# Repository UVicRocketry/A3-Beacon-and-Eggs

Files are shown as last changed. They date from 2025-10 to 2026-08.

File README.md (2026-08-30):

# A3 Beacon and Eggs

Hardware design files (KiCad 9) for the A3 recovery beacon — a VHF transmitter
stitched to the main recovery shock chord.

<p align="center">
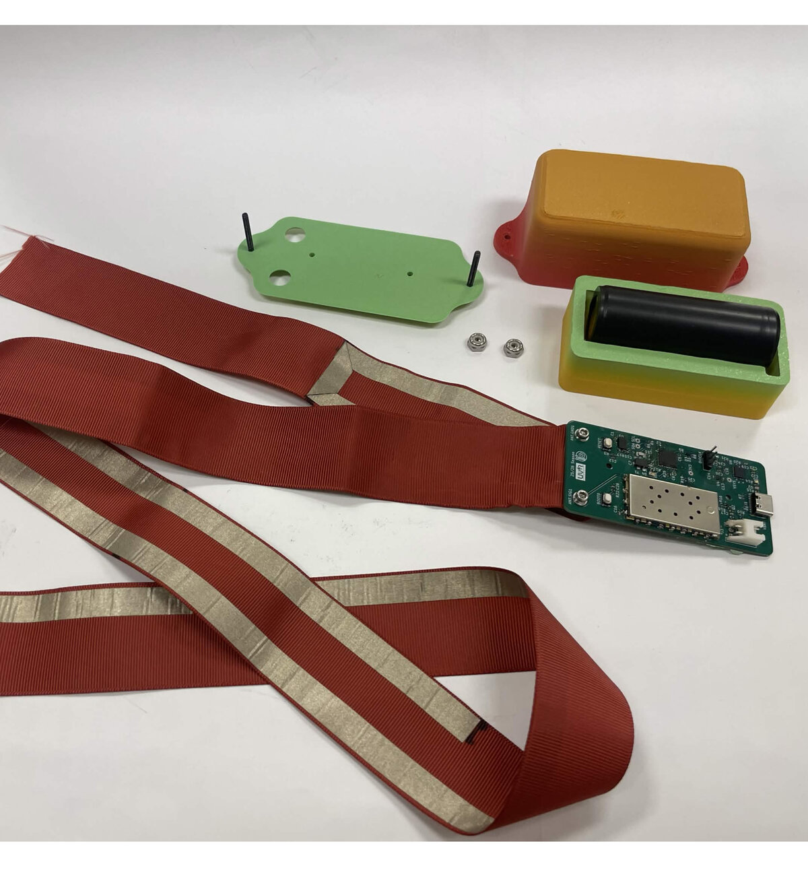
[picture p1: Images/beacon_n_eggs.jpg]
Assembled V1 beacon bolted to its fabric antenna strap, with the printed enclosure and 18650 holder
  
</p>

## Boards

### `Beacon_and_eggs/` — V1 (fabricated)

40 × 80 mm, 4-layer (F.Cu / GND / PWR / B.Cu).

- **MCU** — STM32F411CEU6 with 25 MHz and 32.768 kHz crystals, SWD header,
  boot/reset circuits, and test points
- **Radio** — SA868S / SA818V VHF module, UART control at 9600 baud, with
  TX_EN and TX_PWR_DN control lines and a TX audio input
- **Sensor** — ADXL343 accelerometer on I²C (ALT ADDRESS tied high → 0x1D)
- **Power** — BQ24070 Li-ion charger, USB-C input with ESD clamps, MIC5528
  3.3 V LDO, NTA4151P / NTA4153N load switches, and a divider for battery
  voltage monitoring on the ADC
- **Antenna** — plated mounting holes serve as the RF feed and ground clamp
  for a fabric antenna. 
- Status LEDs, battery connector, and an interactive BOM under `bom/`

### `Beacon_and_eggs_V2/` — in progress

A condensed second revision. Planned:

- Moved to low frequency LoRa Module with Semtech's SX1278
- Move to a smaller Battery
- PIC MCU to interface with transmitter

WIP

### `Beacon BNC Adapter PCB/`

Two-connector coax breakout, used to attach a standard antenna or analyzer to
the beacon's bare antenna pads for bench testing.

## Firmware

Lives in the separate [A3_Beacon_and_Eggs_FW](https://github.com/zgsdlv/A3_Beacon_and_Eggs_FW)
repository (STM32CubeMX + HAL). It is bring-up code only, written to check that
the V1 hardware works - it reads the accelerometer's ID register, handshakes
with the SA868S, and blinks out which of the two responded.

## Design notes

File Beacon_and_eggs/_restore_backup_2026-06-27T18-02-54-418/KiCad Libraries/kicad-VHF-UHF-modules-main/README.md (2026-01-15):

This repository contains symbols, footprints and a 3D model for VHF/UHF modules such as the Dorji [DRA818V](https://www.dorji.com/products-detail.php?ProId=55)/[DRA818U](https://www.dorji.com/products-detail.php?ProId=56) and the SA818, SA818S, SA686 and SA868S modules by [NiceRF](https://www.nicerf.com/).

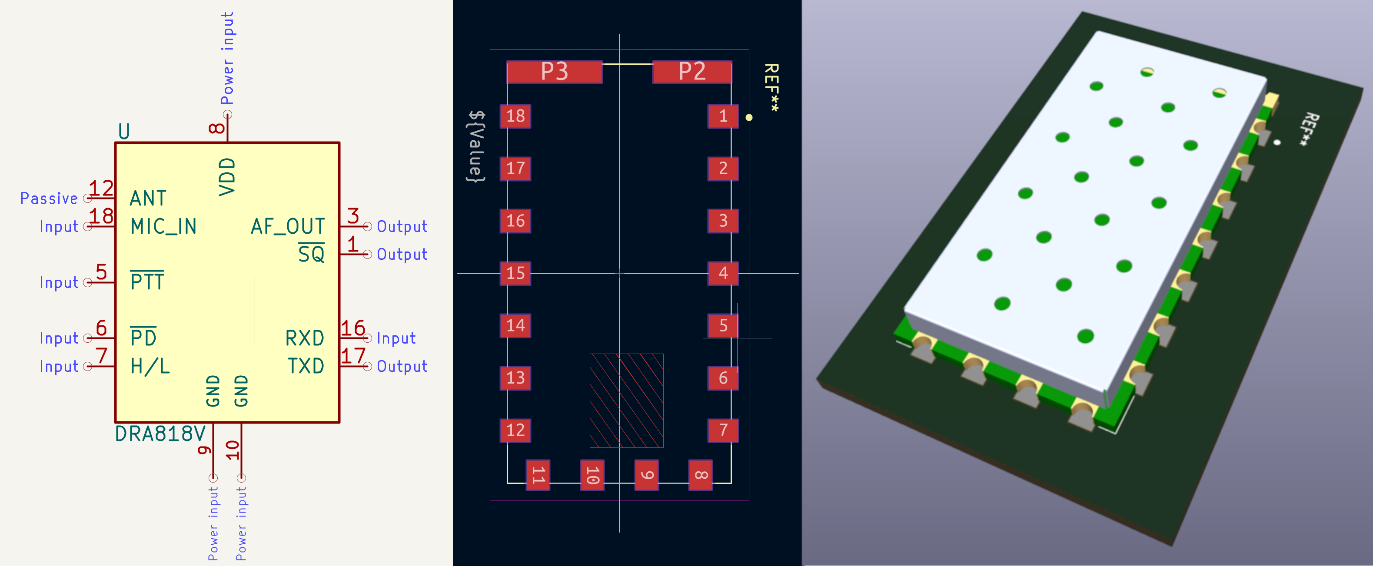
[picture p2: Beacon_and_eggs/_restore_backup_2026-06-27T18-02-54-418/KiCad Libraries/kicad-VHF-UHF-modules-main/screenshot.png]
Screenshots


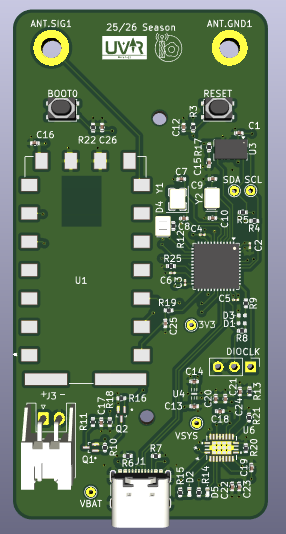
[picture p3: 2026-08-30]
Images/Beacon_and_eggs_3D_View.png

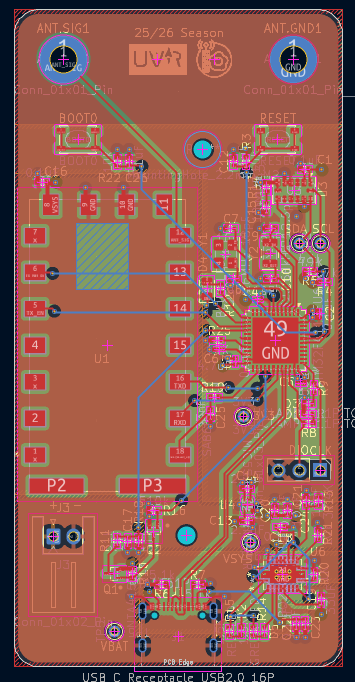
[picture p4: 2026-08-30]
Images/Beacon_PCB_Layout.png

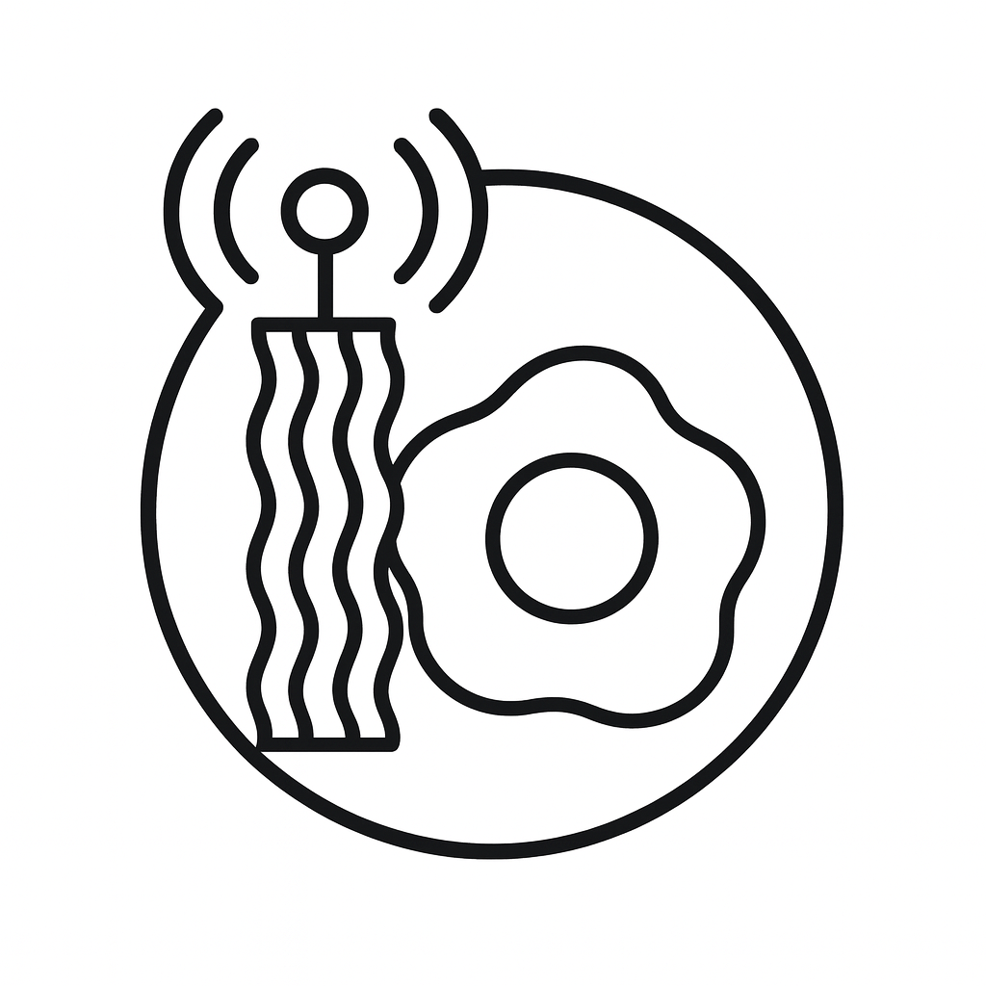
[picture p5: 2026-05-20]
Beacon_and_eggs/_restore_backup_2026-06-27T18-02-54-418/Images/beacon_and_eggs.png

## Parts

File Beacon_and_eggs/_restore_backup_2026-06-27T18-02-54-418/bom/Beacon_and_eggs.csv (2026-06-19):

Id | Designator | Footprint | Quantity | Designation | Supplier and ref
1 |  |  | 1
2 | ANT.GND1, ANT.SIG1 | MountingHole_3.2mm_M3_DIN965_Pad_TopBottom | 2 | Conn_01x01_Pin
3 | BOOT0 | SW_SPST_PTS810 | 1 | BOOT0
4 | C1, C12, C16, C18, C20, C22, C26 | C_0402_1005Metric | 7 | 0.1uF
5 | C2, C3, C4, C5 | C_0201_0603Metric | 4 | 0.1uF
6 | C6 | C_0201_0603Metric | 1 | 4.7uF
7 | C7, C8 | C_0402_1005Metric | 2 | 16pF
8 | C9, C10 | C_0402_1005Metric | 2 | 5pF
9 | C13, C14 | C_0402_1005Metric | 2 | 2.2uF
10 | C15, C21, C23 | C_0402_1005Metric | 3 | 10uF
11 | C17 | C_0402_1005Metric | 1 | 1nF
12 | C19 | C_0402_1005Metric | 1 | 33uF
13 | C24 | C_0402_1005Metric | 1 | 10nF
14 | C25 | C_0402_1005Metric | 1 | 33nF
15 | D1, D3 | D_0402_1005Metric | 2 | UCLAMP3311P.TCT
16 | D2 | LED_0402_1005Metric | 1 | RED LED
17 | D4 | LED_0805_2012Metric | 1 | BLUE LED
18 | D5 | LED_0402_1005Metric | 1 | GREEN LED
19 | J1 | USB_C_Receptacle_GCT_USB4105-xx-A_16P_TopMnt_Horizontal | 1 | USB_C_Receptacle_USB2.0_16P
20 | J3 | JST_XH_S2B-XH-A_1x02_P2.50mm_Horizontal | 1 | Conn_01x02_Pin
21 | Q1 | SOT50P160X90-3N | 1 | NTA4151P
22 | Q2 | SOT50P160X90-3N | 1 | NTA4153N
23 | R3, R21, R22 | R_0402_1005Metric | 3 | 10k
24 | R4, R5 | R_0402_1005Metric | 2 | 4.7k
25 | R6, R7 | R_0402_1005Metric | 2 | 5.1k
26 | R8, R9, R12 | R_0402_1005Metric | 3 | 250R
27 | R10, R11, R18 | R_0402_1005Metric | 3 | 51k
28 | R13 | R_0402_1005Metric | 1 | 37.4K
29 | R14, R15 | R_0402_1005Metric | 2 | 1.5K
30 | R16 | R_0402_1005Metric | 1 | 510k
31 | R17 | R_0402_1005Metric | 1 | 50R
32 | R19 | R_0402_1005Metric | 1 | 3.3K
33 | R20 | R_0402_1005Metric | 1 | 1K
34 | R25 | R_0402_1005Metric | 1 | 10K
35 | RESET | SW_SPST_PTS810 | 1 | RESET
36 | U1 | VHF_UHF_Module_generic | 1 | SA868S
37 | U2 | QFN-48-1EP_7x7mm_P0.5mm_EP5.6x5.6mm | 1 | STM32F411CEU6TR
38 | U3 | LGA-14_3x5mm_P0.8mm_LayoutBorder1x6y | 1 | ADXL343
39 | U4 | XTDFN6_1P2X1P2_MCH | 1 | MIC5528-3.3YMX-TR
40 | U6 | RHL20_2P05X3P05 | 1 | BQ24070RHLR
41 | Y1 | Crystal_SMD_Abracon_ABM8G-4Pin_3.2x2.5mm | 1 | 25MHz 18pF
42 | Y2 | Crystal_SMD_EuroQuartz_EQ161-2Pin_3.2x1.5mm | 1 | 32.768kHz 12.5pF

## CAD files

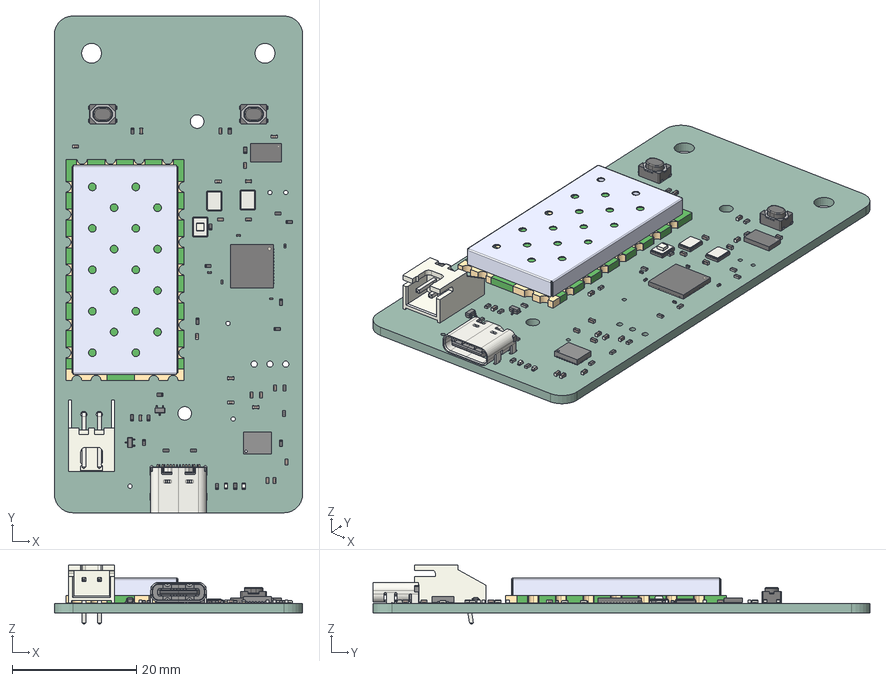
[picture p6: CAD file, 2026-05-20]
Beacon_and_eggs/_restore_backup_2026-06-27T18-02-54-418/beacon_board.step
40.0 x 80.0 x 9.50 mm
JST_S2B_XH_A
C_0402_1005Metric x 20
R_0402_1005Metric x 21
LED_0402_1005Metric x 2
C_0201_0603Metric x 5
DTC115TET1G x 2
LGA_14_3x5mm_P08mm_LayoutBorder1x6y
QFN-48-1EP_7x7mm_Pitch0.5mm
SW_SPST_PTS810 x 2
Crystal_SMD_Abracon_ABM8G-4Pin_3.2x2.5mm
RHL20
LED_0805_2012Metric
Crystal_SMD_EuroQuartz_MT-4Pin_3.2x2.5mm_HandSoldering x 2
USB_C_Receptacle_16P_TopMnt_Horizontal_GCT_USB4105-xx-A
DRA818V
Beacon_and_eggs_PCB

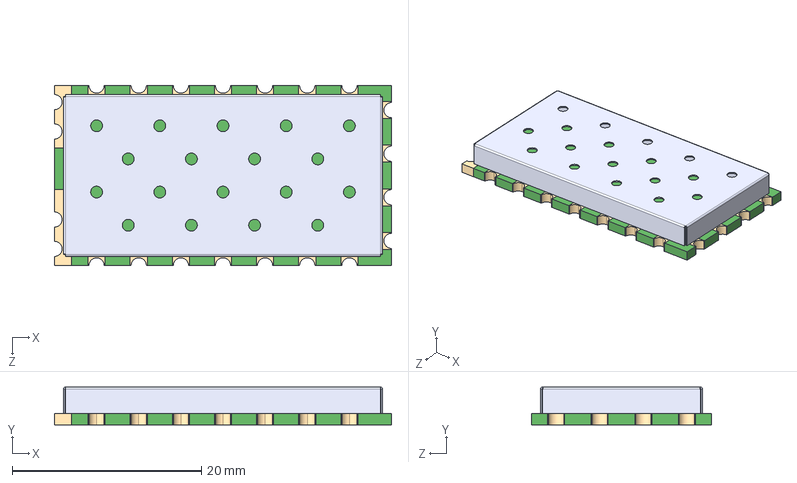
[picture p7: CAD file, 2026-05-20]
Beacon_and_eggs/_restore_backup_2026-06-27T18-02-54-418/KiCad Libraries/kicad-VHF-UHF-modules-main/DRA818V.step
35.6 x 4.00 x 19.0 mm

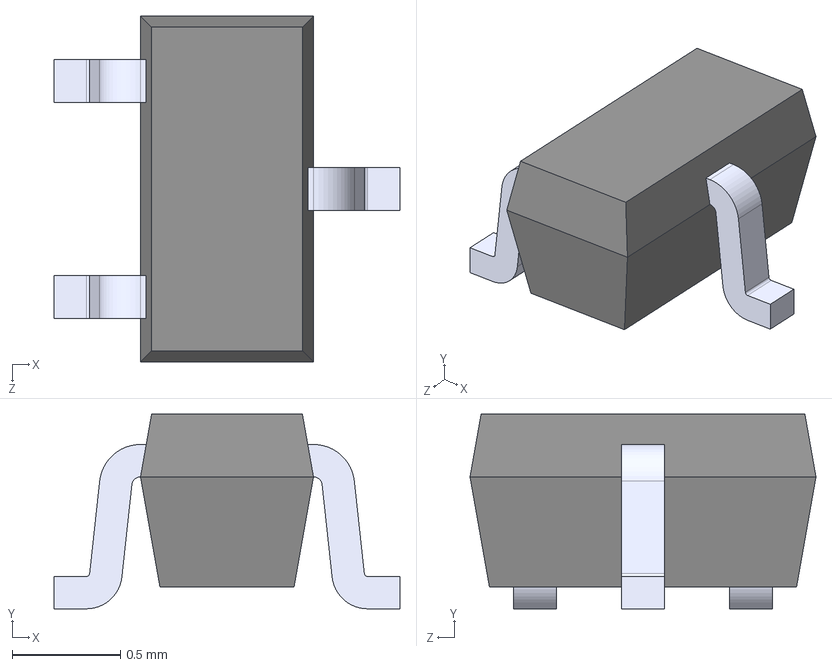
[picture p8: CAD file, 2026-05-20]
Beacon_and_eggs/_restore_backup_2026-06-27T18-02-54-418/KiCad Libraries/NTA4151PT1G/NTA4151PT1G.STEP
1.60 x 0.9 x 1.60 mm

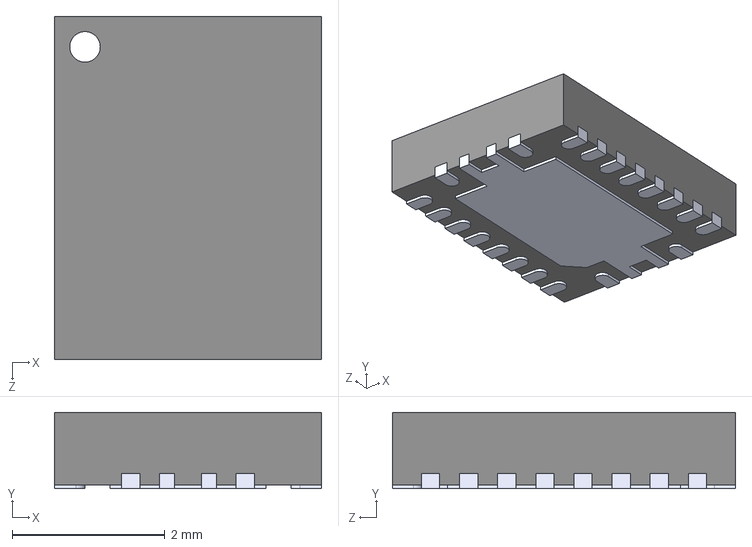
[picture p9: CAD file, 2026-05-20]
Beacon_and_eggs/_restore_backup_2026-06-27T18-02-54-418/KiCad Libraries/BQ24070RHLR/KiCADv6/BQ24070RHLR.STEP
3.50 x 1.00 x 4.50 mm

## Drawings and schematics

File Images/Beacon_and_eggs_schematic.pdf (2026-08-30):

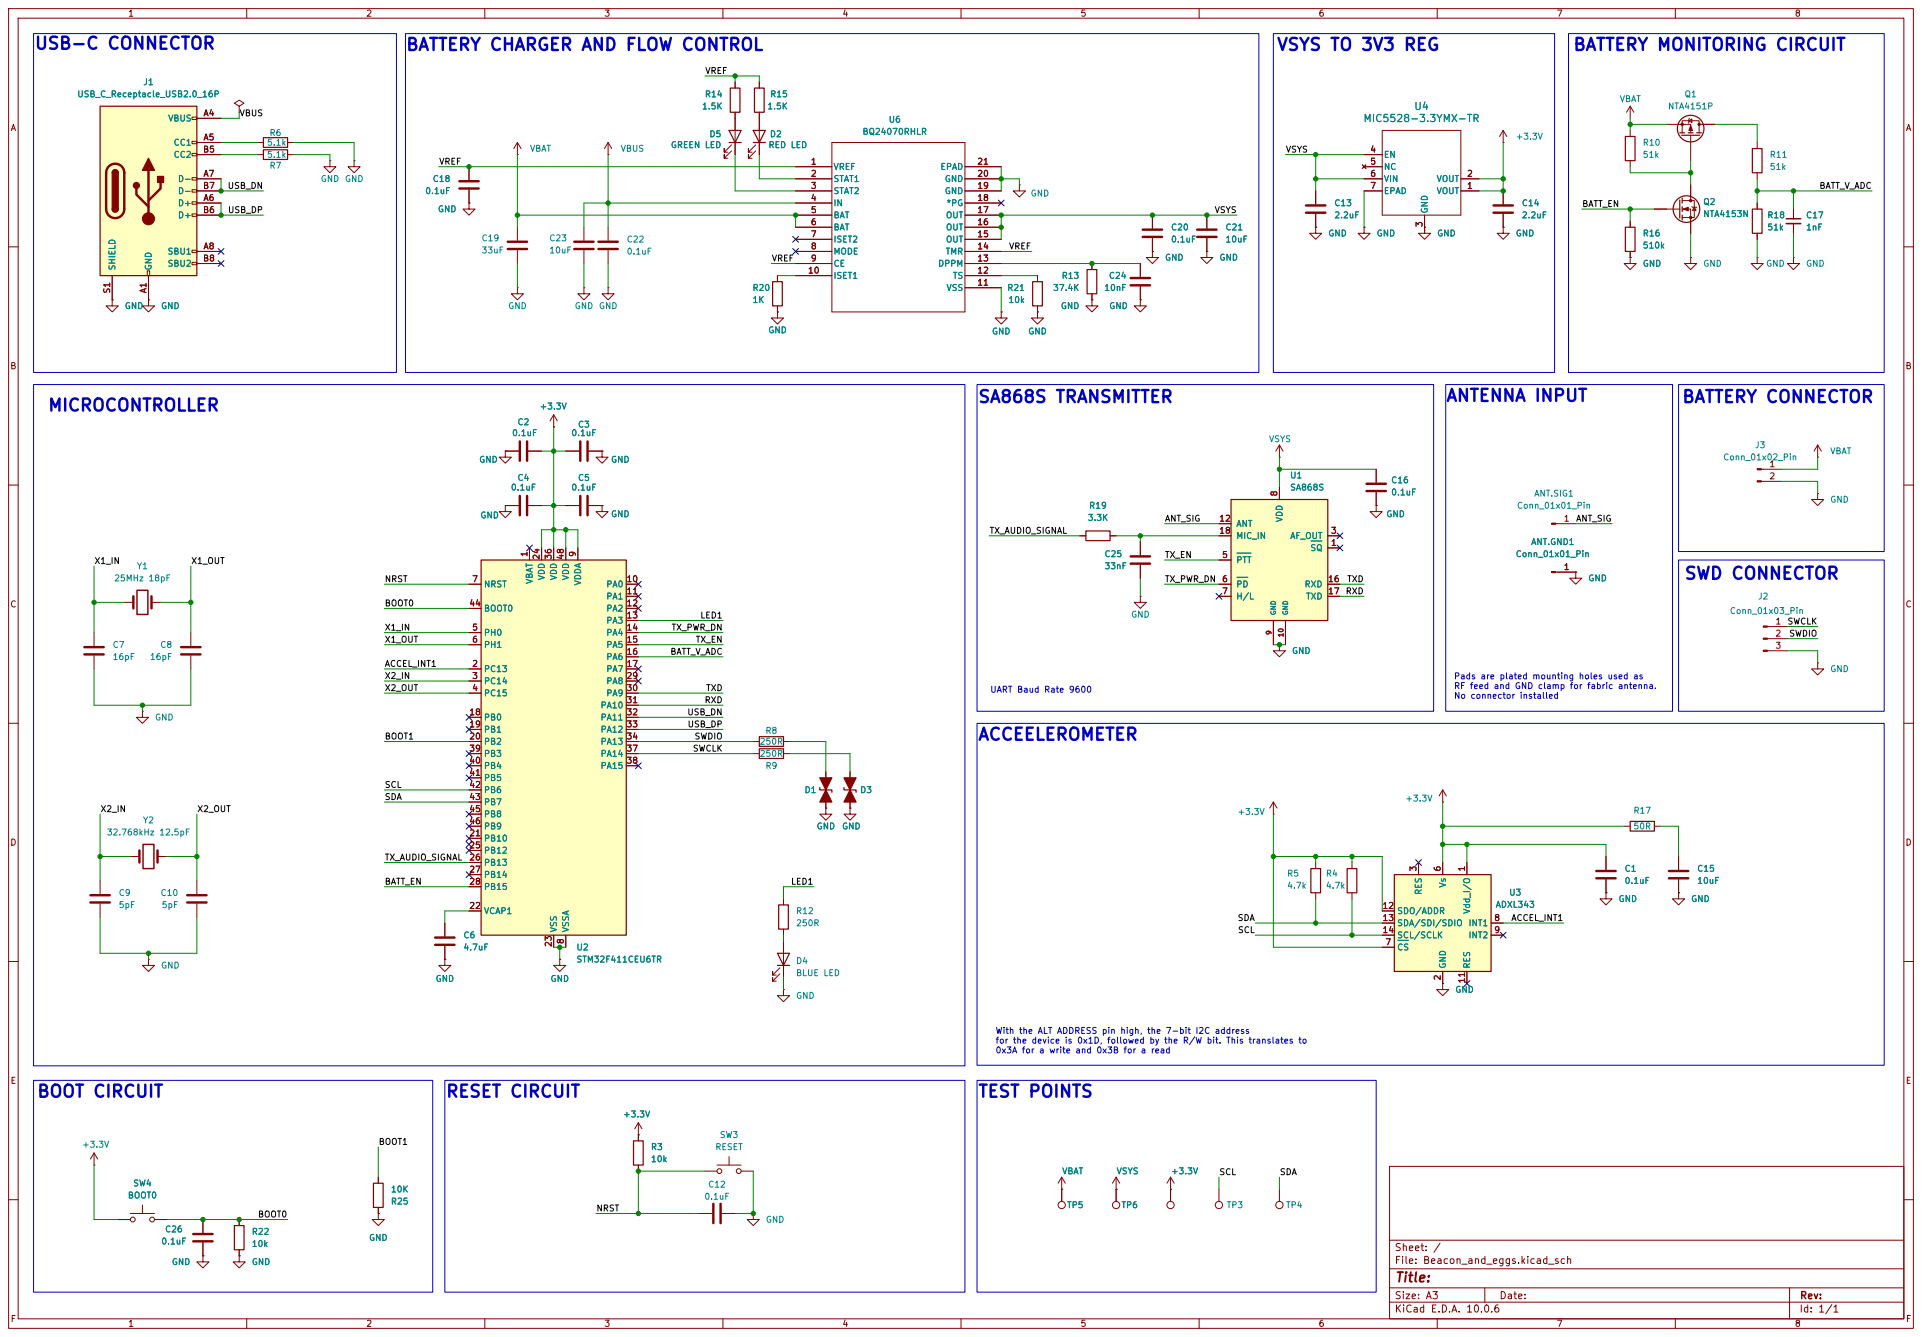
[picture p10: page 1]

BATTERY CHARGER AND FLOW CONTROL

Pads are plated mounting holes used as RF feed and GND clamp for fabric antenna. No connector installed UART Baud Rate 9600 R3

With the ALT ADDRESS pin high, the 7-bit I2C address
for the device is 0x1D, followed by the R/W bit. This translates to 0x3A for a write and 0x3B for a read

Size: A3 | Rev: | F Date:
KiCad E.D.A. 10.0.6 | Id: 1/1

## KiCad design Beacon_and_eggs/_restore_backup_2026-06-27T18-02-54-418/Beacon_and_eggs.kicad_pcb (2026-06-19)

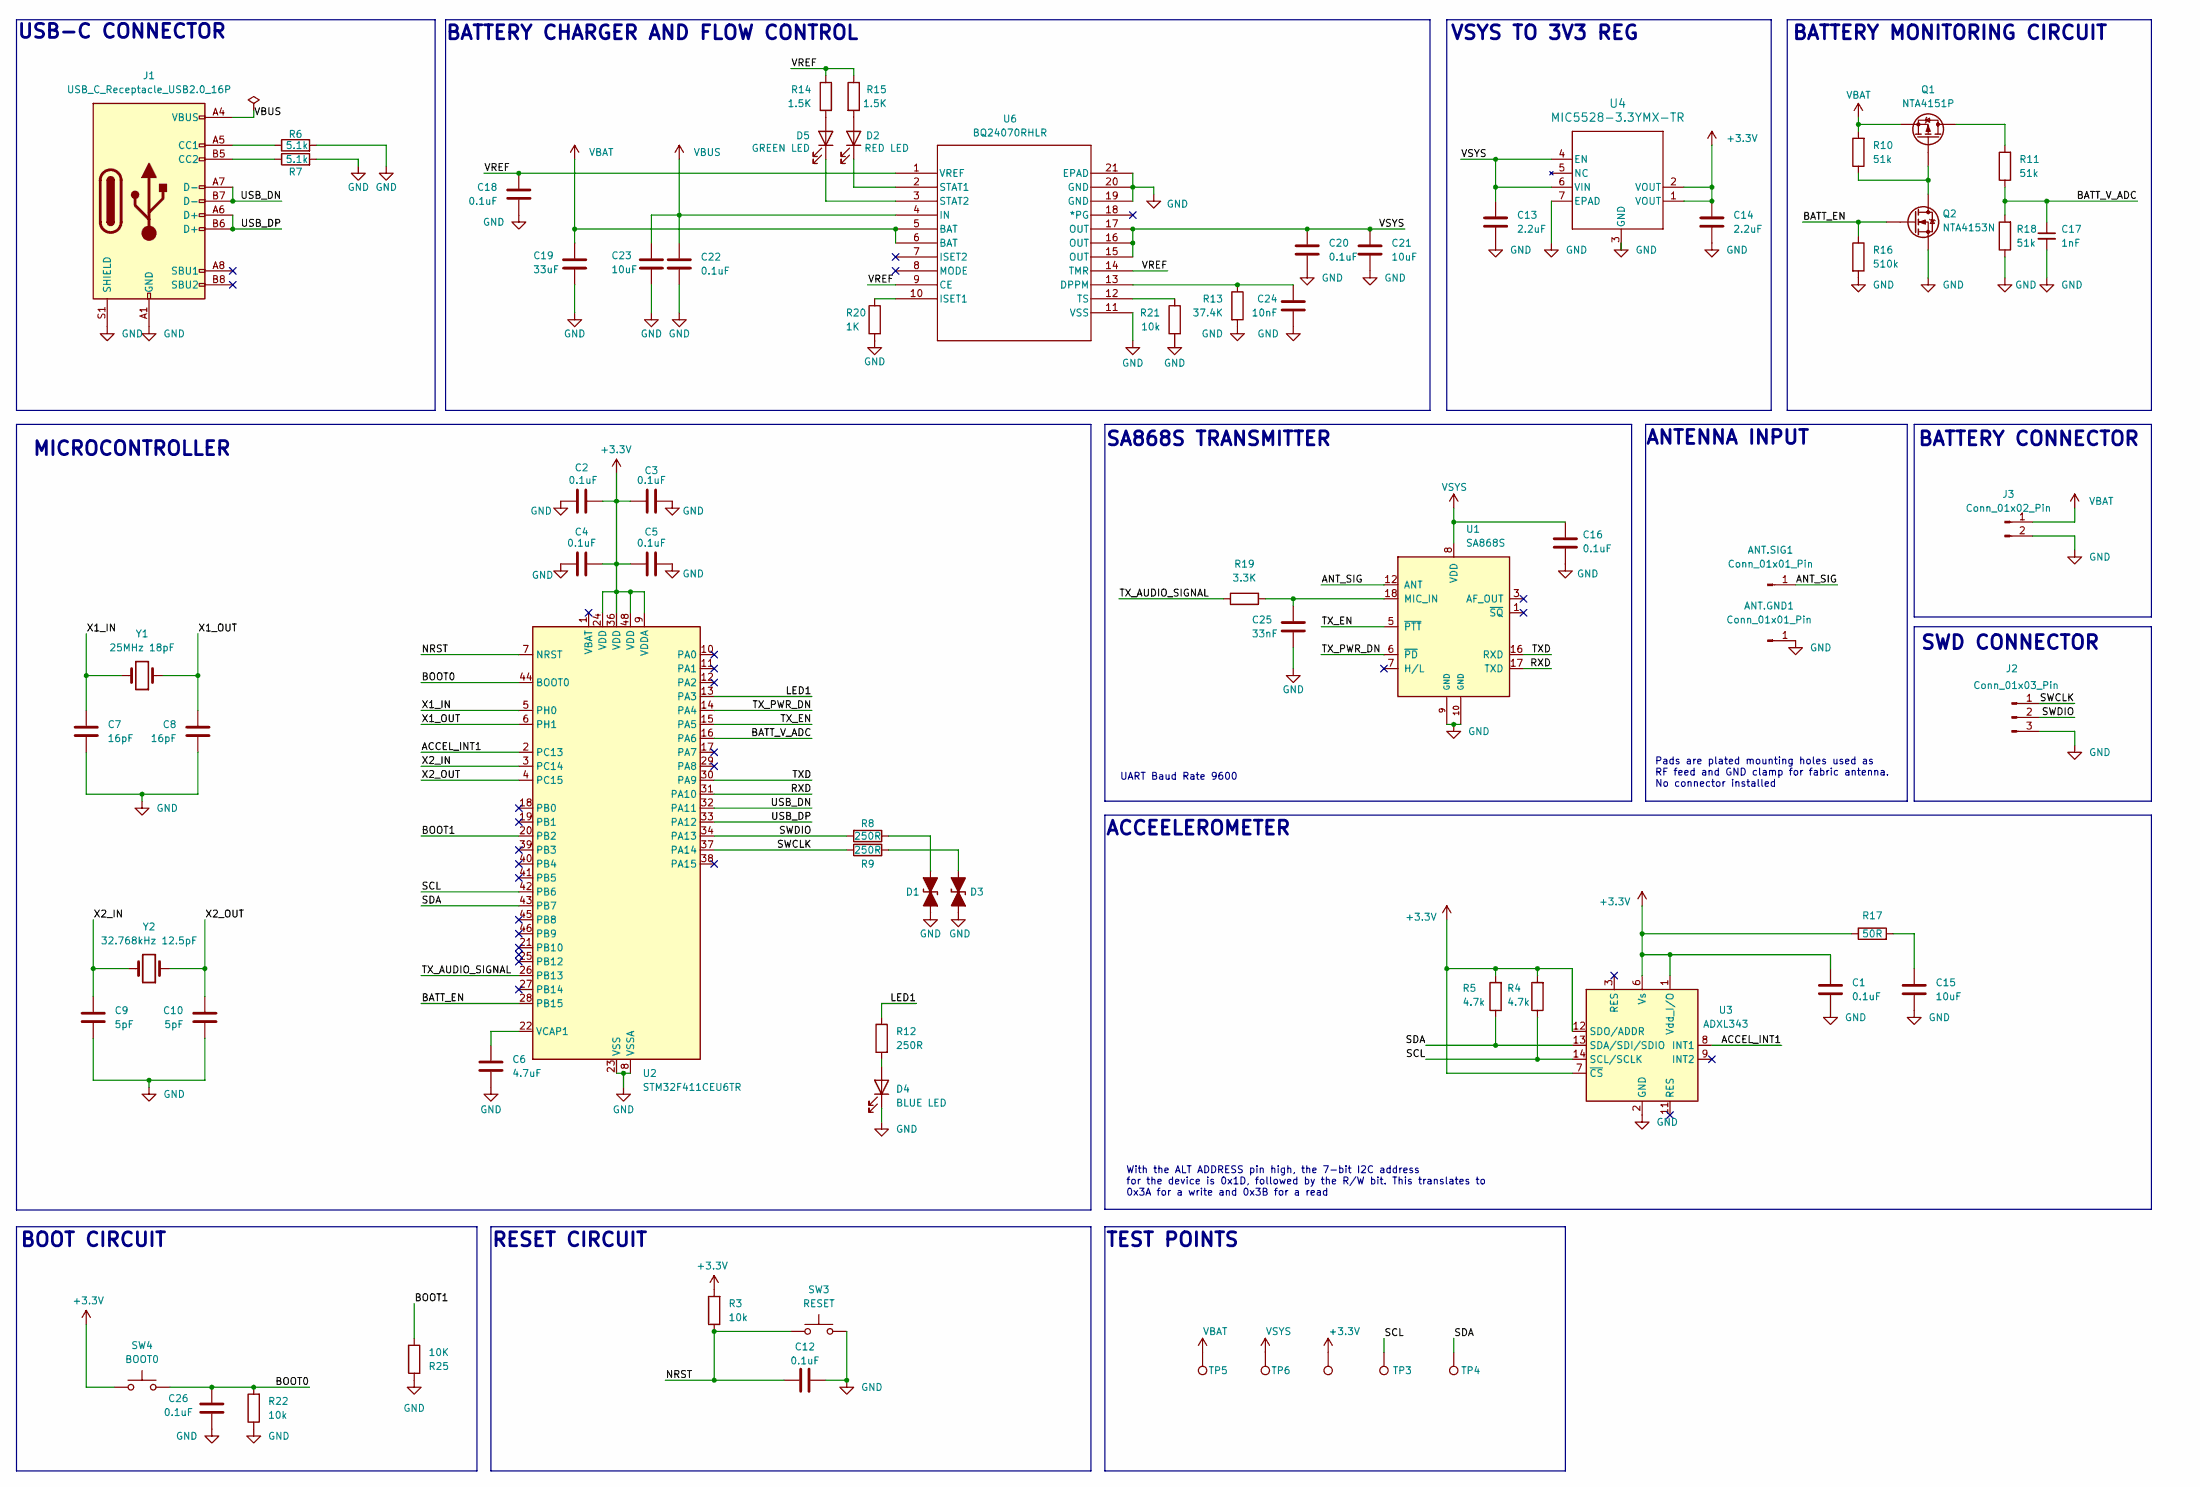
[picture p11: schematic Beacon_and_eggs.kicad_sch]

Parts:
3V3: 3V3; TestPoint_THTPad_D1.5mm_Drill0.7mm
ANT.GND1, ANT.SIG1: Conn_01x01_Pin; MountingHole_3.2mm_M3_DIN965_Pad_TopBottom
C1, C12, C16, C18, C20, C22, C26: 0.1uF; C_0402_1005Metric; DigiKey_Part_Number C0402C104K4RACTU
C2, C3, C4, C5: 0.1uF; C_0201_0603Metric; DigiKey_Part_Number GRM033C71C104KE14D
C6: 4.7uF; C_0201_0603Metric; DigiKey_Part_Number GRM035R60J475ME15J
C7, C8: 16pF; C_0402_1005Metric; DigiKey_Part_Number GJM1555C1H160FB01J
C9, C10: 5pF; C_0402_1005Metric; DigiKey_Part_Number GRM1555C1H5R0BA01D
C13, C14: 2.2uF; C_0402_1005Metric; DigiKey_Part_Number GRM155C80J225KE95D
C15, C21, C23: 10uF; C_0402_1005Metric; DigiKey_Part_Number GRM155R61A106ME11D
C17: 1nF; C_0402_1005Metric; Digikey Part Number 1292-1621-1-ND
C19: 33uF; C_0402_1005Metric; DigiKey_Part_Number GRM155R60J156ME15D
C24: 10nF; C_0402_1005Metric; DigiKey_Part_Number GRM155R71C103KA01D
C25: 33nF; C_0402_1005Metric; DigiKey_Part_Number C0402C333J4RACTU
D1, D3: UCLAMP3311P.TCT; D_0402_1005Metric; Manufacturer Part Number UCLAMP3311P.TCT; Digikey Part Number UCLAMP3311PCT-ND
D2: RED LED; LED_0402_1005Metric; DigiKey_Part_Number SML-D12U1WT86
D4: BLUE LED; LED_0805_2012Metric; DigiKey_Part_Number 150080BS75000
D5: GREEN LED; LED_0402_1005Metric; DigiKey_Part_Number 150060GS75000
J1: USB_C_Receptacle_USB2.0_16P; USB_C_Receptacle_GCT_USB4105-xx-A_16P_TopMnt_Horizontal; DigiKey_Part_Number USB4215-03-A
J2: Conn_01x03_Pin; PinHeader_1x03_P2.54mm_Vertical
J3: Conn_01x02_Pin; JST_XH_S2B-XH-A_1x02_P2.50mm_Horizontal
Q1: NTA4151P; SOT50P160X90-3N; Manufacturer Part Number NTA4151PT1G; Digikey Part Number NTA4151PT1GOSCT-ND
Q2: NTA4153N; SOT50P160X90-3N; Manufacturer Part Number NTA4153NT1G; Digikey Part Number NTA4153NT1GOSCT-ND
R3, R21, R22: 10k; R_0402_1005Metric; DigiKey_Part_Number RMCF0402FT10K0
R4, R5: 4.7k; R_0402_1005Metric; DigiKey_Part_Number RC0402JR-074K7L
R6, R7: 5.1k; R_0402_1005Metric; DigiKey_Part_Number RC0402FR-075K1L
R8, R9, R12: 250R; R_0402_1005Metric; DigiKey_Part_Number RE0402BRE07250RL
R10, R11, R18: 51k; R_0402_1005Metric; Digikey Part Number 311-51.0KMCT-ND
R13: 37.4K; R_0402_1005Metric; DigiKey_Part_Number ERJ-2RKF3742X
R14, R15: 1.5K; R_0402_1005Metric; DigiKey_Part_Number RC0402FR-071K5L
R16: 510k; R_0402_1005Metric; Digikey Part Number YAG2713CT-ND
R17: 50R; R_0402_1005Metric; DigiKey_Part_Number RT0402BRE0750RL
R19: 3.3K; R_0402_1005Metric; DigiKey_Part_Number ERA-2AEB332X
R20: 1K; R_0402_1005Metric; DigiKey_Part_Number RC0402FR-071KL
R25: 10K; R_0402_1005Metric; DigiKey_Part_Number RMCF0402FT10K0
SW3: RESET; SW_SPST_PTS810; DigiKey_Part_Number PTS810SJK250SMTR LFS
SW4: BOOT0; SW_SPST_PTS810; DigiKey_Part_Number PTS810SJK250SMTR LFS
TP3: SCL; TestPoint_THTPad_D1.5mm_Drill0.7mm
TP4: SDA; TestPoint_THTPad_D1.5mm_Drill0.7mm
TP5: VBAT; TestPoint_THTPad_D1.5mm_Drill0.7mm
TP6: VSYS; TestPoint_THTPad_D1.5mm_Drill0.7mm
U1: SA868S; VHF_UHF_Module_generic; DigiKey_Part_Number SA868S
U2: STM32F411CEU6TR; QFN-48-1EP_7x7mm_P0.5mm_EP5.6x5.6mm; DigiKey_Part_Number STM32F411CEU6TR
U3: ADXL343; LGA-14_3x5mm_P0.8mm_LayoutBorder1x6y; DigiKey_Part_Number ADXL343BCCZ-RL7
U4: MIC5528-3.3YMX-TR; XTDFN6_1P2X1P2_MCH; DigiKey_Part_Number MIC5528-3.3YMX-TR
U6: BQ24070RHLR; RHL20_2P05X3P05; PARTREV 4219071/A 05/2017; DigiKey_Part_Number 296-19652-1-ND
Y1: 25MHz 18pF; Crystal_SMD_Abracon_ABM8G-4Pin_3.2x2.5mm; DigiKey_Part_Number ABM3-25.000MHZ-D2Y-T
Y2: 32.768kHz 12.5pF; Crystal_SMD_EuroQuartz_EQ161-2Pin_3.2x1.5mm; DigiKey_Part_Number 12.87167

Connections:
+3.3V: 3V3.1 (1_1), C1.1, C2.2, C3.1, C4.2, C5.1, C14.1, R3.2, R4.2, R5.2, R17.1, SW4.3 (B), SW4.4 (B), U2.9 (VDDA), U2.24 (VDD), U2.36 (VDD), U2.48 (VDD), U3.1 (Vdd_I/O), U3.6 (Vs), U3.7 (~CS), U3.12 (SDO/ADDR), U4.1 (VOUT), U4.2 (VOUT)
/ACCEL_INT1: U2.2 (PC13), U3.8 (INT1)
/ANT_SIG: ANT.SIG1.1 (Pin_1_1), U1.12 (ANT)
/BATT_EN: Q2.1 (G), R16.1, U2.28 (PB15)
/BATT_V_ADC: C17.1, R11.1, R18.2, U2.16 (PA6)
/BOOT0: C26.1, R22.2, SW4.1 (A), SW4.2 (A), U2.44 (BOOT0); also elsewhere on the board
/BOOT1: R25.2, U2.20 (PB2)
/LED1: R12.1, U2.13 (PA3)
/NRST: C12.1, R3.1, SW3.1 (A), SW3.2 (A), U2.7 (NRST); also elsewhere on the board
/RXD: U1.17 (TXD), U2.31 (PA10)
/SCL: R4.1, TP3.1 (1_1), U2.42 (PB6), U3.14 (SCL/SCLK)
/SDA: R5.1, TP4.1 (1_1), U2.43 (PB7), U3.13 (SDA/SDI/SDIO)
/SWCLK: J2.1, R9.1, U2.37 (PA14)
/SWDIO: J2.2, R8.2, U2.34 (PA13)
/TXD: U1.16 (RXD), U2.30 (PA9)
/TX_AUDIO_SIGNAL: R19.1, U2.26 (PB13)
/TX_EN: U1.5 (~PTT), U2.15 (PA5)
/TX_PWR_DN: U1.6 (~PD), U2.14 (PA4)
/USB_DN: J1.A7 (D-), J1.B7 (D-), U2.32 (PA11)
/USB_DP: J1.A6 (D+), J1.B6 (D+), U2.33 (PA12)
/VREF: C18.1, R14.1, R15.1, U6.1 (VREF), U6.9 (CE), U6.14 (TMR)
/X1_IN: C7.2, U2.5 (PH0), Y1.2
/X1_OUT: C8.2, U2.6 (PH1), Y1.1
/X2_IN: C9.2, U2.3 (PC14), Y2.2
/X2_OUT: C10.2, U2.4 (PC15), Y2.1
GND: ANT.GND1.1 (Pin_1_1), C1.2, C2.1, C3.2, C4.1, C5.2, C6.1, C7.1, C8.1, C9.1, C10.1, C12.2, C13.2, C14.2, C15.2, C16.2, C17.2, C18.2, C19.2, C20.2, C21.2, C22.2, C23.2, C24.2, C25.2, C26.2, D1.1 (A1), D3.1 (A1), D4.1 (K), J1.A1 (GND), J1.A12 (GND), J1.B1 (GND), J1.B12 (GND), J1.S1 (SHIELD), J1.SH, J2.3, J3.2, Q2.2 (S), R6.2, R7.2, R13.2, R16.2, R18.1, R20.2, R21.2, R22.1, R25.1, SW3.3 (B), SW3.4 (B), U1.9 (GND), U1.10 (GND), U2.8 (VSSA), U2.23 (VSS), U2.35 (VSS), U2.47 (VSS), U2.49 (VSS), U3.2 (GND), U3.4 (GND), U3.5 (GND), U4.3 (GND), U4.7 (EPAD), U6.11 (VSS), U6.19 (GND), U6.20 (GND), U6.21 (EPAD), U6.V
unnamed: C15.1, R17.2
unnamed: D1.2 (A2), R8.1
unnamed: D2.2 (A), R15.2
unnamed: D2.1 (K), U6.2 (STAT1)
unnamed: D3.2 (A2), R9.2
unnamed: D4.2 (A), R12.2
unnamed: D5.2 (A), R14.2
unnamed: D5.1 (K), U6.3 (STAT2)
unnamed: J1.A5 (CC1), R6.1
unnamed: J1.B5 (CC2), R7.1
unnamed: Q1.3 (D1), Q1.8 (D1), R11.2
unnamed: Q1.1 (G1), Q2.3 (D), R10.1
unnamed: C25.1, R19.2, U1.18 (MIC_IN)
unnamed: C6.2, U2.22 (VCAP1)
unnamed: C24.1, R13.1, U6.13 (DPPM)
unnamed: R20.1, U6.10 (ISET1)
unnamed: R21.1, U6.12 (TS)
VBAT: C19.1, J3.1, Q1.2 (S1), R10.2, TP5.1 (1_1), U6.5 (BAT), U6.6 (BAT)
VBUS: C22.1, C23.1, J1.A4 (VBUS), J1.A9 (VBUS), J1.B4 (VBUS), J1.B9 (VBUS), U6.4 (IN)
VSYS: C13.1, C16.1, C20.1, C21.1, TP6.1 (1_1), U1.8 (VDD), U4.4 (EN), U4.6 (VIN), U6.15 (OUT), U6.16 (OUT), U6.17 (OUT)

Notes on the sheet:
BATTERY CONNECTOR
SWD CONNECTOR
RESET CIRCUIT
BOOT CIRCUIT
TEST POINTS
VSYS TO 3V3 REG
SA868S TRANSMITTER
With the ALT ADDRESS pin high, the 7-bit I2C address for the device is 0x1D, followed by the R/W bit. This translates to 0x3A for a write and 0x3B for a read
BATTERY CHARGER AND FLOW CONTROL
USB-C CONNECTOR
Pads are plated mounting holes used as RF feed and GND clamp for fabric antenna. No connector installed
UART Baud Rate 9600
ACCEELEROMETER
ANTENNA INPUT
BATTERY MONITORING CIRCUIT
MICROCONTROLLER

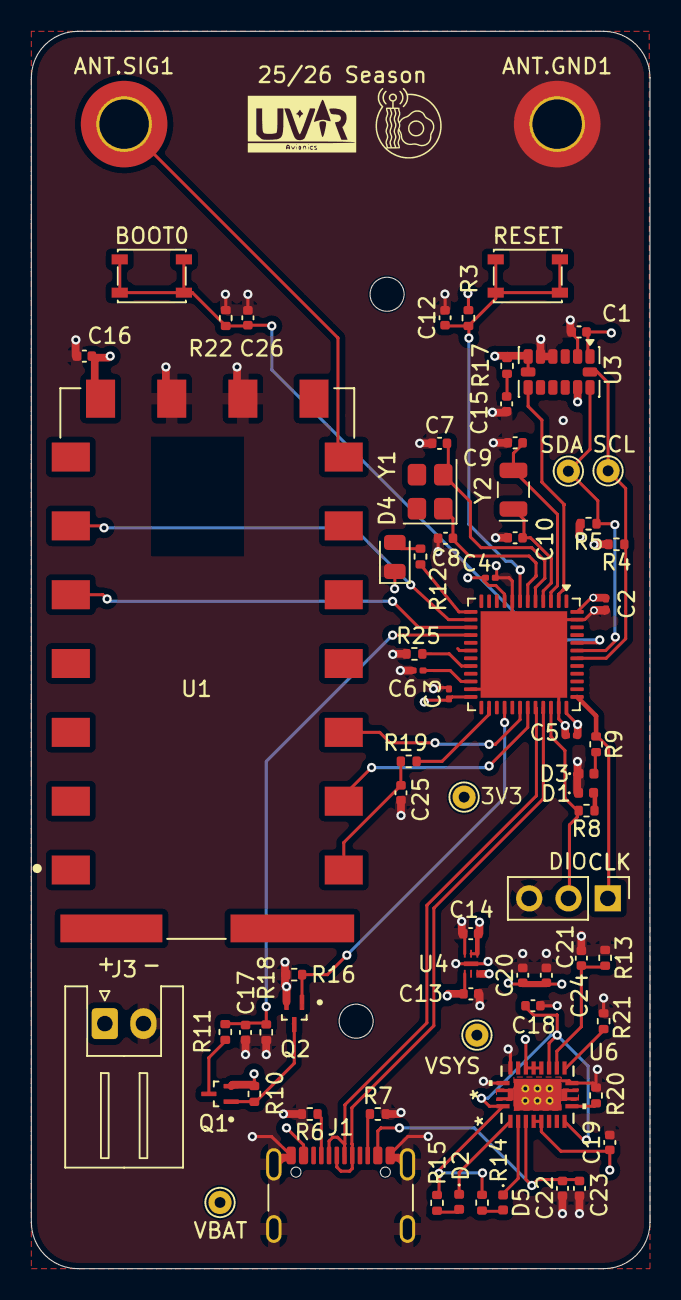
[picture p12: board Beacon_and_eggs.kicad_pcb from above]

Board: 4 copper layers, 40.0 x 80.0 mm, 72 parts (0 on the bottom side), 46 nets.

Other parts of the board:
BOOT0: BOOT0; SW_SPST_PTS810
RESET: RESET; SW_SPST_PTS810

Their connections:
/BOOT0: BOOT0.1 (A), BOOT0.2 (A); also elsewhere on the board
/NRST: RESET.1 (A), RESET.2 (A); also elsewhere on the board

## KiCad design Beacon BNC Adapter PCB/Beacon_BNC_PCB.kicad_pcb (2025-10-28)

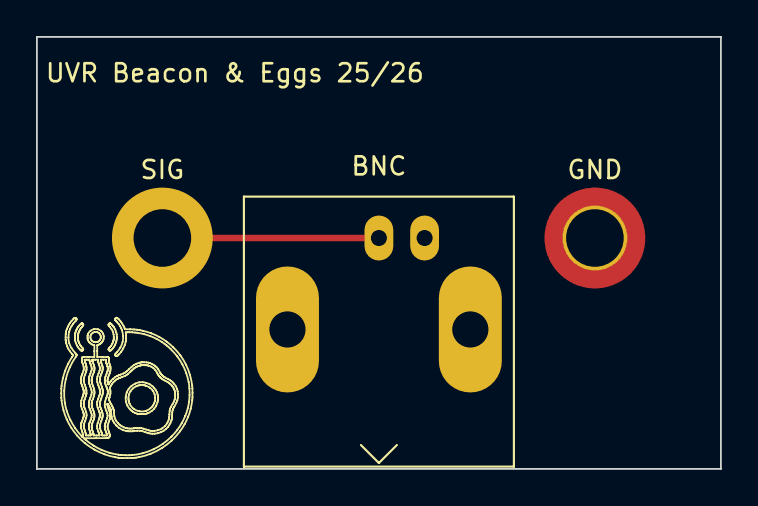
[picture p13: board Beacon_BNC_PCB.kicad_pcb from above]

Board: 2 copper layers, 38.0 x 24.0 mm, 3 parts (0 on the bottom side), 2 nets.

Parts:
BNC: Conn_Coaxial; BNC_Amphenol_B6252HB-NPP3G-50_Horizontal
GND: MountingHole_3.2mm_M3_DIN965_Pad_TopBottom
SIG: MountingHole_3.2mm_M3_DIN965_Pad_TopBottom

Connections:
/GND: BNC.2 (Ext), GND.1
/RF_IN: BNC.1 (In), SIG.1

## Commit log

2025-10-26 initial commit, adding BNC Adapter PCBfolder.
    [Beacon_BNC_PCB.kicad_pcb, Beacon_BNC_PCB.kicad_sch]
2025-10-26 added folder
    [Beacon_BNC_PCB.kicad_pcb, Beacon_BNC_PCB.kicad_sch]
2025-10-28 increased trace width to .36 and added gerber files
    [Beacon_BNC_PCB.kicad_pcb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]
2025-11-25 Uploading KiCAD files
    Yeet
    [Beacon_and_eggs.kicad_pcb, Beacon_and_eggs.kicad_sch]
2025-11-26 Reorganization
    Whoot (reorganized the placement of the newly added voltage circuitry, SA868, and ADXL343)
    [Beacon_and_eggs.kicad_sch]
2026-01-13 Reformatted Schematic Layout
    cool beans
    [Beacon_and_eggs.kicad_sch]
2026-01-14 Implemented new boost/buck converter
    [Beacon_and_eggs.kicad_sch]
2026-01-14 Buzzer, USB, and Documentation
    Added the buzzer and USB c circuits, alongside adding boxes with labels to the remaining parts of the circuit
    [Beacon_and_eggs.kicad_sch]
2026-01-14 relabeled some global tags
    [Beacon_and_eggs.kicad_sch]
2026-01-15 Assingned most components(1206 for resistors and Capacitors)
    [Beacon_and_eggs.kicad_sch]
2026-01-15 Organized components to be placed tomorrow
    [Beacon_and_eggs.kicad_pcb]
2026-01-15 Started layout process, still needs tracing..
    [Beacon_and_eggs.kicad_pcb, Beacon_and_eggs.kicad_sch]
2026-01-15 Revert "Organized components to be placed tomorrow"
    This reverts commit c4bd26fadb75ae4865d41ebab2e9036565b38f13.
    [Beacon_and_eggs.kicad_pcb]
2026-01-15 Revert "Assingned most components(1206 for resistors and Capacitors)"
    This reverts commit 7557e7a7bd89896b141ef55f24d0591e6209fe46.
    [Beacon_and_eggs.kicad_sch]
2026-01-16 resolved merge issue
    [Beacon_and_eggs.kicad_sch]
2026-01-16 Laid traces and changed 3.3V regulator
    [Beacon_and_eggs.kicad_pcb, Beacon_and_eggs.kicad_sch]
2026-02-09 cheanged schematic and V1 pcb layout completed.
    [Beacon_and_eggs.kicad_pcb, Beacon_and_eggs.kicad_sch]
2026-02-10 narrowed the pcb down from 60mm to 40 mm
    [Beacon_and_eggs.kicad_pcb, Beacon_and_eggs.kicad_sch]
2026-02-10 added missing via net labels
    [Beacon_and_eggs.kicad_pcb]
2026-05-07 Added complete BOM, replaced a footprint, added missing STEP files
    [Beacon_and_eggs.kicad_pcb, Beacon_and_eggs.kicad_sch]
2026-05-09 edited silkscreen text
    [Beacon_and_eggs.kicad_pcb]
2026-05-14 fixed accel. pinouts, added 10k resistor to TS of U6
    [Beacon_and_eggs.kicad_pcb, Beacon_and_eggs.kicad_sch]
2026-05-15 added step file for enclosure design
    [beacon_board.step]
2026-05-16 reduce drc error to 0, updated step file
    [Beacon_and_eggs.kicad_pcb, Beacon_and_eggs.kicad_sch, beacon_board.step]
2026-05-16 changed batery connector footprint from vert. to horz.
    [Beacon_and_eggs.kicad_pcb, Beacon_and_eggs.kicad_sch]
2026-05-19 updated step file
    [beacon_board.step]
2026-05-20 updated step file, added 3D components
    [BQ24070RHLR.STEP, Beacon_and_eggs.kicad_pcb, Beacon_and_eggs.kicad_sch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]
2026-05-20 changed UART software pins to hardware pins, fixed I2C pins
    [Beacon_and_eggs.kicad_pcb, Beacon_and_eggs.kicad_sch]
2026-05-27 labelled switches
    [Beacon_and_eggs.kicad_pcb, Beacon_and_eggs.kicad_sch]
2026-05-28 added manufacturing files
    [Beacon_and_eggs.kicad_pcb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]
2026-05-28 reattempting to add manufacturing files
    [Beacon_and_eggs-B_Cu.gbr, Beacon_and_eggs-B_Mask.gbr, Beacon_and_eggs-B_Paste.gbr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]
2026-05-28 file clean up
    [Beacon_and_eggs-B_Cu.gbr, Beacon_and_eggs-B_Mask.gbr, Beacon_and_eggs-B_Paste.gbr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]
2026-06-19 Updated two digipart numbers and remade BOM
    [Beacon_and_eggs.csv, Beacon_and_eggs.kicad_pcb, Beacon_and_eggs.kicad_sch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]
